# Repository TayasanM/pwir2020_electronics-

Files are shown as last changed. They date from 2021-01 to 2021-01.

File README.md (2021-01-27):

# pwir2020_Madmax_Electronics-
## Functionality Discription  
This electronic board consists of the main control circuit and driver circuit.  
  
This circuit capable of driver three DC Gear Motors (16V)  
  
and communicate with the onboard computer via USB connection execute Motor rotation is given speed and give feedback of speed.  
  
Another functionality of this board is controlling thrower servo Motor speed.  
  
Driver Motor speed control using PI controller implement in firmware to archive desired speed quickly  
## Communication  
Communication between the main PC and control board happens in HEX values(16 bits).  
driver Motor speeds send between 0-100, thrower Motors speed (0-1000) and end command  
  
Motor1_speed,Motor2_speed,Motor3_speed,Thrower_speed,command_end  
  
E.g. 64 00 64 00 64 00 64 00 AA AA  
  
## Connection ##  
- Micro USB: Communicate with PC where you can get speeds of the speeds of the motors and send feedback
- J7         : STM32 programmer connector  
	- 1 : +3.3V
	- 2 :SWDIO(communication with programmer)
	- 4 :SWCLK(Progrmamer clock)    
	- 10:NRST(reset)
	-  3,5,9:GND
	- 6,7,8: NC

- J5         : Driver Motor2 encoder conector
	- 1 : GND	    
	- 2 :+3.3V
	- 3 : Encoder Signal line 2 for Motor2
	- 4 : Encoder Signal line 1 for Motor2
             
- J6         : Driver Motor3 encoder conector
	- 1 : GND
	- 2 :+3.3V
	- 3 : Encoder Signal line 2 for Motor3
	- 4 : Encoder Signal line 1 for Motor3)
- J4         : Driver Motor1 encoder conector  
	- 1 : GND
	- 2 :+3.3V 
	- 3 : Encoder Signal line 2 for Motor1
	- 4 : Encoder Signal line 1 for Motor1
- J3         : Thrower Motor Signal connector
	-  1 : GND
	-  2  :PWM
	-  3 : NC 
	-  4 : NC
- U2         : Driver Motor1 power connector
- U3         : Driver Motor2 power connector
- U4         : Driver Motor3 power connector
- '+'          : Driver Motor powerconnection (battery 16V)
- '+'          : Driver Motor powerconnection (battery 16V)

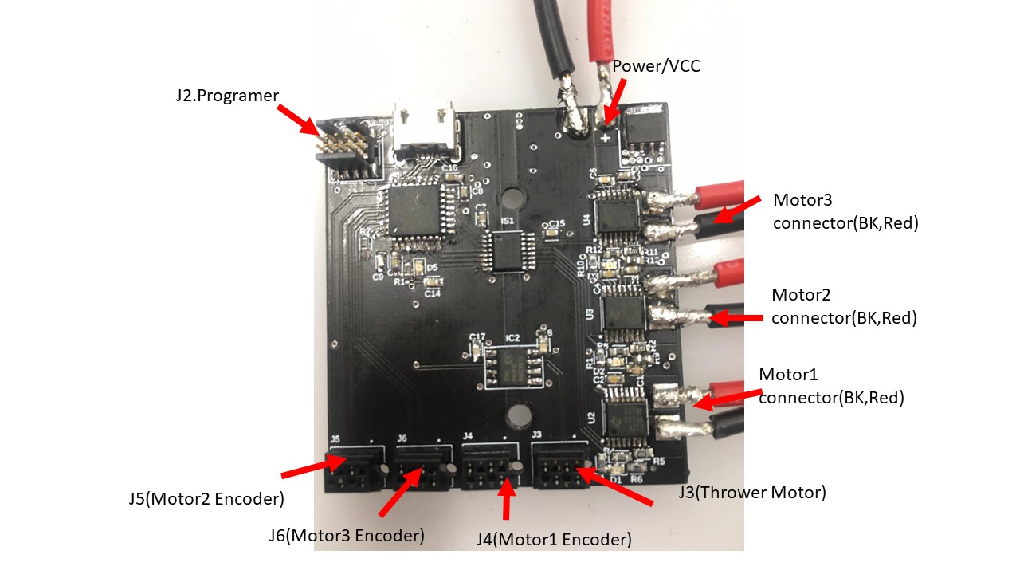
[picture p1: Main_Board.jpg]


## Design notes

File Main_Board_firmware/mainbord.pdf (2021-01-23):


07/12/2020

## mainbord Project Configuration Report

# 1. Description

## 1.1. Project

Project Name | mainbord
Board Name | custom
Generated with: | STM32CubeMX 6.0.0
Date | 12/07/2020

## 1.2. MCU

MCU Series | STM32G4
MCU Line | STM32G4x1
MCU name | STM32G431KBTx
MCU Package | LQFP32
MCU Pin number | 32

## 1.3. Core(s) information

Core(s) | ARM Cortex-M4

# 2. Pinout Configuration

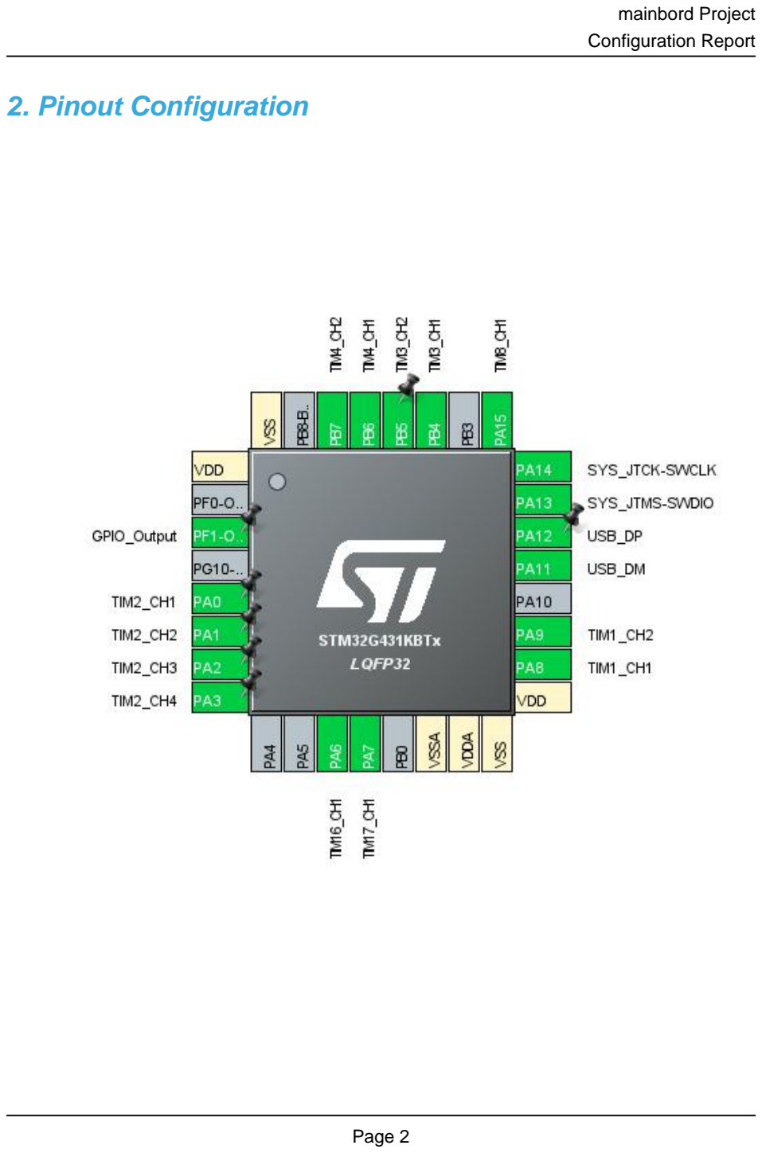
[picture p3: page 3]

# 3. Pins Configuration

Pin Number LQFP32 | Pin Name (function after reset) | Pin Type | Alternate Function(s) | Label
1 | VDD | Power
3 | PF1-OSC_OUT * | I/O | GPIO_Output
5 | PA0 | I/O | TIM2_CH1
6 | PA1 | I/O | TIM2_CH2
7 | PA2 | I/O | TIM2_CH3
8 | PA3 | I/O | TIM2_CH4
11 | PA6 | I/O | TIM16_CH1
12 | PA7 | I/O | TIM17_CH1
14 | VSSA | Power
15 | VDDA | Power
16 | VSS | Power
17 | VDD | Power
18 | PA8 | I/O | TIM1_CH1
19 | PA9 | I/O | TIM1_CH2
21 | PA11 | I/O | USB_DM
22 | PA12 | I/O | USB_DP
23 | PA13 | I/O | SYS_JTMS-SWDIO
24 | PA14 | I/O | SYS_JTCK-SWCLK
25 | PA15 | I/O | TIM8_CH1
27 | PB4 | I/O | TIM3_CH1
28 | PB5 | I/O | TIM3_CH2
29 | PB6 | I/O | TIM4_CH1
30 | PB7 | I/O | TIM4_CH2
32 | VSS | Power

## * The pin is affected with an I/O function

# 4. Clock Tree Configuration

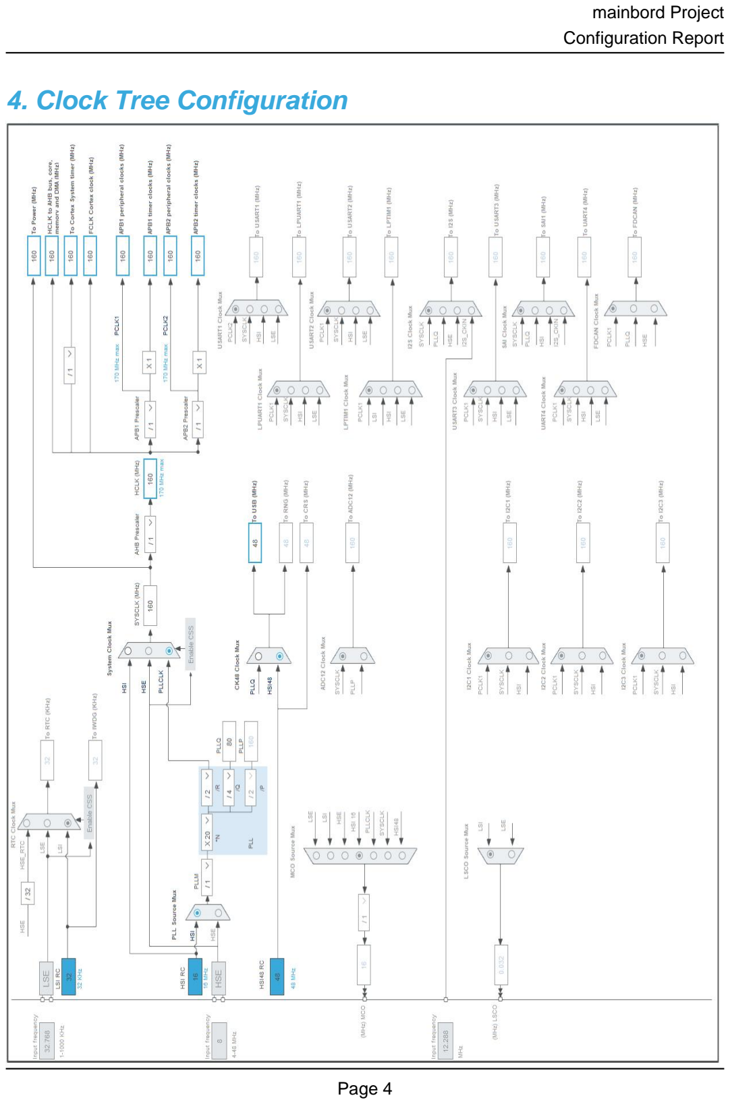
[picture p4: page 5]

# 5. Software Project

## 5.1. Project Settings

Name | Value
Project Name | mainbord
Project Folder | C:\Users\Dell\STM32CubeIDE\workspace_1.4.0\mainbord
Toolchain / IDE | STM32CubeIDE
Firmware Package Name and Version | STM32Cube FW_G4 V1.3.0
Application Structure | Advanced
Generate Under Root | Yes
Do not generate the main() | No
Minimum Heap Size | 0x200
Minimum Stack Size | 0x400

## 5.2. Code Generation Settings

Name | Value
STM32Cube MCU packages and embedded software | Copy only the necessary library files
Generate peripheral initialization as a pair of '.c/.h' files | No
Backup previously generated files when re-generating | No
Keep User Code when re-generating | Yes
Delete previously generated files when not re-generated | Yes
Set all free pins as analog (to optimize the power consumption) | No
Enable Full Assert | No

## 5.3. Advanced Settings - Generated Function Calls

Rank | Function Name | IP Instance Name
1 | MX_GPIO_Init | GPIO
2 | SystemClock_Config | RCC
3 | MX_TIM2_Init | TIM2
4 | MX_TIM3_Init | TIM3
5 | MX_TIM4_Init | TIM4
6 | MX_TIM7_Init | TIM7
7 | MX_TIM8_Init | TIM8
8 | MX_TIM1_Init | TIM1
9 | MX_TIM16_Init | TIM16
10 | MX_TIM17_Init | TIM17
11 | MX_USB_Device_Init | USB_DEVICE

Rank | Function Name | IP Instance Name
12 | MX_TIM6_Init | TIM6

# 6. Power Consumption Calculator report

## 6.1. Microcontroller Selection

Series | STM32G4
Line | STM32G4x1
MCU | STM32G431KBTx
Datasheet | DS12589_Rev0

## 6.2. Parameter Selection

Temperature | 25
Vdd | 3.0

## 6.3. Battery Selection

Battery | Li-SOCL2(A3400)
Capacity | 3400.0 mAh
Self Discharge | 0.08 %/month
Nominal Voltage | 3.6 V
Max Cont Current | 100.0 mA
Max Pulse Current | 200.0 mA
Cells in series | 1
Cells in parallel | 1

## 6.4. Sequence

Step | Step1 | Step2
Mode | RUN | STOP1
Vdd | 3.0 | 3.0
Voltage Source | Battery | Battery
Range | Range1-Boost | NoRange
Fetch Type | FLASH/ART | NA
CPU Frequency | 170 MHz | 0 Hz
Clock Configuration | HSE BYP PLL | ALL CLOCKS OFF
Clock Source Frequency | 4 MHz | 0 Hz

### Peripherals

Additional Cons. | 0 mA | 0 mA
Average Current | 25.5 mA | 59 µA
Duration | 0.1 ms | 0.9 ms
DMIPS | 213.0 | 0.0
Ta Max | 124.19 | 129.99
Category | In DS Table | In DS Table

## 6.5. Results

Sequence Time | 1 ms | Average Current | 2.6 mA
Battery Life | 1 month, 23 days, 22 hours | Average DMIPS | 212.5 DMIPS

## 6.6. Chart

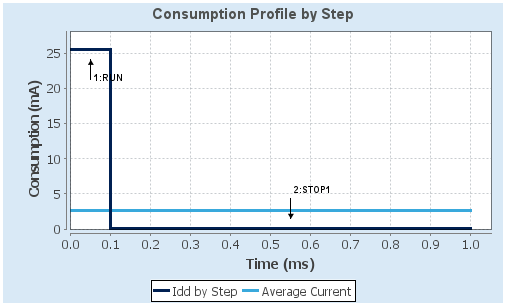
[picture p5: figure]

# 7. IPs and Middleware Configuration

## 7.1. GPIO

## 7.2. RCC

## 7.2.1. Parameter Settings:

### System Parameters:

VDD voltage (V) | 3.3
Instruction Cache | Enabled
Prefetch Buffer | Disabled
Data Cache | Enabled
Flash Latency(WS) | 4 WS (5 CPU cycle)

### RCC Parameters:

HSI Calibration Value | 64
HSE Startup Timout Value (ms) | 100
LSE Startup Timout Value (ms) | 5000

### Power Parameters:

Power Regulator Voltage Scale | Power Regulator Voltage Scale 1 boost

### Peripherals Clock Configuration:

Generate the peripherals clock configuration | TRUE

## 7.3. SYS Debug: Serial Wire Timebase Source: SysTick mode: save power of non-active UCPD - deactive Dead Battery pull-up

## 7.4. TIM1 Combined Channels: Encoder Mode

## 7.4.1. Parameter Settings:

### Counter Settings:

Prescaler (PSC - 16 bits value) | 0
Counter Mode | Up
Dithering | Disable
Counter Period (AutoReload Register - 16 bits value ) | 65535
Internal Clock Division (CKD) | No Division
Repetition Counter (RCR - 16 bits value) | 0

auto-reload preload | Disable

### Trigger Output (TRGO) Parameters:

Master/Slave Mode (MSM bit) | Disable (Trigger input effect not delayed)
Trigger Event Selection TRGO | Reset (UG bit from TIMx_EGR)
Trigger Event Selection TRGO2 | Reset (UG bit from TIMx_EGR)

### Pulse On Compare ( Common for Channel 3 and 4 ):

Pulse Width Prescaler | 0
Pulse Width | 0

### Encoder:

Encoder Mode | Encoder Mode TI1 and TI2 *
Slave Mode Preload Activation | Disable
____ Parameters for Channel 1 ____
Polarity | Rising Edge
IC Selection | Direct
Prescaler Division Ratio | No division
Input Filter | 0
____ Parameters for Channel 2 ____
Polarity | Rising Edge
IC Selection | Direct
Prescaler Division Ratio | No division
Input Filter | 0

## 7.5. TIM2 Channel1: PWM Generation CH1 Channel2: PWM Generation CH2 Channel3: PWM Generation CH3 Channel4: PWM Generation CH4

## 7.5.1. Parameter Settings:

### Counter Settings:

Prescaler (PSC - 16 bits value) | 0
Counter Mode | Up
Dithering | Disable
Counter Period (AutoReload Register - 32 bits value ) | 65535 *
Internal Clock Division (CKD) | No Division
auto-reload preload | Disable

### Trigger Output (TRGO) Parameters:

Master/Slave Mode (MSM bit) | Disable (Trigger input effect not delayed)
Trigger Event Selection TRGO | Reset (UG bit from TIMx_EGR)

### Clear Input:

Clear Input Source | Disable

### Pulse On Compare ( Common for Channel 3 and 4 ):

Pulse Width Prescaler | 0
Pulse Width | 0

### PWM Generation Channel 1:

Mode | PWM mode 1
Pulse (32 bits value) | 0
Output compare preload | Enable
Fast Mode | Disable
CH Polarity | High

### PWM Generation Channel 2:

Mode | PWM mode 1
Pulse (32 bits value) | 0
Output compare preload | Enable
Fast Mode | Disable
CH Polarity | High

### PWM Generation Channel 3:

Mode | PWM mode 1
Pulse (32 bits value) | 0
Output compare preload | Enable
Fast Mode | Disable
CH Polarity | High

### PWM Generation Channel 4:

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

## 7.6. TIM3 Combined Channels: Encoder Mode

## 7.6.1. Parameter Settings:

### Counter Settings:

Prescaler (PSC - 16 bits value) | 0
Counter Mode | Up
Dithering | Disable
Counter Period (AutoReload Register - 16 bits value ) | 65535

Internal Clock Division (CKD) | No Division
auto-reload preload | Disable

### Trigger Output (TRGO) Parameters:

Master/Slave Mode (MSM bit) | Disable (Trigger input effect not delayed)
Trigger Event Selection TRGO | Reset (UG bit from TIMx_EGR)

### Pulse On Compare ( Common for Channel 3 and 4 ):

Pulse Width Prescaler | 0
Pulse Width | 0

### Encoder:

Encoder Mode | Encoder Mode TI1 and TI2 *
Slave Mode Preload Activation | Disable
____ Parameters for Channel 1 ____
Polarity | Rising Edge
IC Selection | Direct
Prescaler Division Ratio | No division
Input Filter | 0
____ Parameters for Channel 2 ____
Polarity | Rising Edge
IC Selection | Direct
Prescaler Division Ratio | No division
Input Filter | 0

## 7.7. TIM4 Combined Channels: Encoder Mode

## 7.7.1. Parameter Settings:

### Counter Settings:

Prescaler (PSC - 16 bits value) | 0
Counter Mode | Up
Dithering | Disable
Counter Period (AutoReload Register - 16 bits value ) | 65535
Internal Clock Division (CKD) | No Division
auto-reload preload | Disable

### Trigger Output (TRGO) Parameters:

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

### Pulse On Compare ( Common for Channel 3 and 4 ):

Pulse Width Prescaler | 0
Pulse Width | 0

### Encoder:

Encoder Mode | Encoder Mode TI1 and TI2 *
Slave Mode Preload Activation | Disable
____ Parameters for Channel 1 ____
Polarity | Rising Edge
IC Selection | Direct
Prescaler Division Ratio | No division
Input Filter | 0
____ Parameters for Channel 2 ____
Polarity | Rising Edge
IC Selection | Direct
Prescaler Division Ratio | No division
Input Filter | 0

## 7.8. TIM6 mode: Activated

## 7.8.1. Parameter Settings:

### Counter Settings:

Prescaler (PSC - 16 bits value) | 24 *
Counter Mode | Up
Dithering | Disable
Counter Period (AutoReload Register - 16 bits value ) | 63999 *
auto-reload preload | Disable

### Trigger Output (TRGO) Parameters:

Trigger Event Selection | Reset (UG bit from TIMx_EGR)

## 7.9. TIM7 mode: Activated

## 7.9.1. Parameter Settings:

### Counter Settings:

Prescaler (PSC - 16 bits value) | 0
Counter Mode | Up
Dithering | Disable
Counter Period (AutoReload Register - 16 bits value ) | 65535
auto-reload preload | Disable

### Trigger Output (TRGO) Parameters:

Trigger Event Selection | Reset (UG bit from TIMx_EGR)

## 7.10. TIM8 Channel1: PWM Generation CH1

## 7.10.1. Parameter Settings:

### Counter Settings:

Prescaler (PSC - 16 bits value) | 0
Counter Mode | Up
Dithering | Disable
Counter Period (AutoReload Register - 16 bits value ) | 65535
Internal Clock Division (CKD) | No Division
Repetition Counter (RCR - 16 bits value) | 0
auto-reload preload | Disable

### Trigger Output (TRGO) Parameters:

Master/Slave Mode (MSM bit) | Disable (Trigger input effect not delayed)
Trigger Event Selection TRGO | Reset (UG bit from TIMx_EGR)
Trigger Event Selection TRGO2 | Reset (UG bit from TIMx_EGR)

### Break And Dead Time management - BRK Configuration:

BRK State | Disable
BRK Polarity | High
BRK Filter (4 bits value) | 0
BRK Sources Configuration
- Digital Input | Disable
- COMP1 | Disable
- COMP2 | Disable
- COMP3 | Disable
- COMP4 | Disable

### Break And Dead Time management - BRK2 Configuration:

BRK2 State | Disable
BRK2 Polarity | High
BRK2 Filter (4 bits value) | 0
BRK2 Sources Configuration
- Digital Input | Disable
- COMP1 | Disable
- COMP2 | Disable
- COMP3 | Disable
- COMP4 | Disable

### Break And Dead Time management - Output Configuration:

Automatic Output State | Disable
Off State Selection for Run Mode (OSSR) | Disable
Off State Selection for Idle Mode (OSSI) | Disable
Lock Configuration | Off

### Clear Input:

Clear Input Source | Disable

### Pulse On Compare ( Common for Channel 3 and 4 ):

Pulse Width Prescaler | 0
Pulse Width | 0

### PWM Generation Channel 1:

Mode | PWM mode 1
Pulse (16 bits value) | 0
Output compare preload | Enable
Fast Mode | Disable
CH Polarity | High
CH Idle State | Reset

## 7.11. TIM16 mode: Activated Channel1: PWM Generation CH1

## 7.11.1. Parameter Settings:

### Counter Settings:

Prescaler (PSC - 16 bits value) | 0
Counter Mode | Up
Dithering | Disable
Counter Period (AutoReload Register - 16 bits value ) | 65535
Internal Clock Division (CKD) | No Division
Repetition Counter (RCR - 8 bits value) | 0
auto-reload preload | Disable

### Break And Dead Time management - BRK Configuration:

BRK State | Disable
BRK Polarity | High
BRK Filter (4 bits value) | 0
BRK Sources Configuration
- Digital Input | Disable
- COMP1 | Disable
- COMP2 | Disable
- COMP3 | Disable
- COMP4 | Disable

### Break And Dead Time management - Output Configuration:

Automatic Output State | Disable
Off State Selection for Run Mode (OSSR) | Disable
Off State Selection for Idle Mode (OSSI) | Disable
Lock Configuration | Off

### PWM Generation Channel 1:

Mode | PWM mode 1
Pulse (16 bits value) | 0
Output compare preload | Enable
Fast Mode | Disable
CH Polarity | High
CH Idle State | Reset

## 7.12. TIM17 mode: Activated Channel1: PWM Generation CH1

## 7.12.1. Parameter Settings:

### Counter Settings:

Prescaler (PSC - 16 bits value) | 0
Counter Mode | Up
Dithering | Disable
Counter Period (AutoReload Register - 16 bits value ) | 65535
Internal Clock Division (CKD) | No Division
Repetition Counter (RCR - 8 bits value) | 0
auto-reload preload | Disable

### Break And Dead Time management - BRK Configuration:

BRK State | Disable
BRK Polarity | High
BRK Filter (4 bits value) | 0
BRK Sources Configuration
- Digital Input | Disable
- COMP1 | Disable
- COMP2 | Disable
- COMP3 | Disable
- COMP4 | Disable

### Break And Dead Time management - Output Configuration:

Automatic Output State | Disable
Off State Selection for Run Mode (OSSR) | Disable
Off State Selection for Idle Mode (OSSI) | Disable

Lock Configuration | Off

### PWM Generation Channel 1:

Mode | PWM mode 1
Pulse (16 bits value) | 0
Output compare preload | Enable
Fast Mode | Disable
CH Polarity | High
CH Idle State | Reset

## 7.13. USB mode: Device (FS)

## 7.13.1. Parameter Settings:

### Basic Parameters:

Speed | Full Speed 12MBit/s
Physical interface | Internal Phy
Sof Enable | Disabled

### Power Parameters:

Low Power | Disabled
Link Power Management | Disabled
Battery Charging | Disabled

## 7.14. USB_DEVICE Class For FS IP: Communication Device Class (Virtual Port Com)

## 7.14.1. Parameter Settings:

### Basic Parameters:

USBD_MAX_NUM_INTERFACES (Maximum number of supported interfaces) | 1
USBD_MAX_NUM_CONFIGURATION (Maximum number of supported configuration) | 1
USBD_MAX_STR_DESC_SIZ (Maximum size for the string descriptors) | 512
USBD_SELF_POWERED (Enabled self power) | Enabled
USBD_DEBUG_LEVEL (USBD Debug Level) | 0: No debug message
USBD_LPM_ENABLED (Link Power Management) | 1: Link Power Management supported

### Class Parameters:

USB CDC Rx Buffer Size | 1000
USB CDC Tx Buffer Size | 1000

## 7.14.2. Device Descriptor:

### Device Descriptor:

VID (Vendor IDentifier) | 1155
LANGID_STRING (Language Identifier) | English(United States)
MANUFACTURER_STRING (Manufacturer Identifier) | STMicroelectronics

### Device Descriptor FS:

PID (Product IDentifier) | 22336
PRODUCT_STRING (Product Identifier) | STM32 Virtual ComPort
CONFIGURATION_STRING (Configuration Identifier) | CDC Config
INTERFACE_STRING (Interface Identifier) | CDC Interface

### * User modified value

# 8. System Configuration

## 8.1. GPIO configuration

IP | Pin | Signal | GPIO mode | GPIO pull/up pull down | Max Speed | User Label
SYS | PA13 | SYS_JTMS-SWDIO | n/a | n/a | n/a
| PA14 | SYS_JTCK-SWCLK | n/a | n/a | n/a
TIM1 | PA8 | TIM1_CH1 | Alternate Function Push Pull | No pull-up and no pull-down | Low
| PA9 | TIM1_CH2 | Alternate Function Push Pull | No pull-up and no pull-down | Low
TIM2 | PA0 | TIM2_CH1 | Alternate Function Push Pull | No pull-up and no pull-down | Low
| PA1 | TIM2_CH2 | Alternate Function Push Pull | No pull-up and no pull-down | Low
| PA2 | TIM2_CH3 | Alternate Function Push Pull | No pull-up and no pull-down | Low
| PA3 | TIM2_CH4 | Alternate Function Push Pull | No pull-up and no pull-down | Low
TIM3 | PB4 | TIM3_CH1 | Alternate Function Push Pull | No pull-up and no pull-down | Low
| PB5 | TIM3_CH2 | Alternate Function Push Pull | No pull-up and no pull-down | Low
TIM4 | PB6 | TIM4_CH1 | Alternate Function Push Pull | No pull-up and no pull-down | Low
| PB7 | TIM4_CH2 | Alternate Function Push Pull | No pull-up and no pull-down | Low
TIM8 | PA15 | TIM8_CH1 | Alternate Function Push Pull | No pull-up and no pull-down | Low
TIM16 | PA6 | TIM16_CH1 | Alternate Function Push Pull | No pull-up and no pull-down | Low
TIM17 | PA7 | TIM17_CH1 | Alternate Function Push Pull | No pull-up and no pull-down | Low
USB | PA11 | USB_DM | n/a | n/a | n/a
| PA12 | USB_DP | n/a | n/a | n/a
GPIO | PF1-OSC_OUT | GPIO_Output | Output Push Pull | No pull-up and no pull-down | Low

## 8.2. DMA configuration

## nothing configured in DMA service

## 8.3. NVIC configuration

## 8.3.1. NVIC

Interrupt Table | Enable | Preenmption Priority | SubPriority
Non maskable interrupt | true | 0 | 0
Hard fault interrupt | true | 0 | 0
Memory management fault | true | 0 | 0
Prefetch fault, memory access fault | true | 0 | 0
Undefined instruction or illegal state | true | 0 | 0
System service call via SWI instruction | true | 0 | 0
Debug monitor | true | 0 | 0
Pendable request for system service | true | 0 | 0
System tick timer | true | 0 | 0
USB low priority interrupt remap | true | 0 | 0
TIM6 global interrupt, DAC1 and DAC3 channel underrun error interrupts | true | 0 | 0
PVD/PVM1/PVM2/PVM3/PVM4 interrupts through EXTI lines 16/38/39/40/41 | unused
Flash global interrupt | unused
RCC global interrupt | unused
USB high priority interrupt remap | unused
TIM1 break interrupt and TIM15 global interrupt | unused
TIM1 update interrupt and TIM16 global interrupt | unused
TIM1 trigger and commutation interrupts and TIM17 global interrupt | unused
TIM1 capture compare interrupt | unused
TIM2 global interrupt | unused
TIM3 global interrupt | unused
TIM4 global interrupt | unused
TIM8 break interrupt | unused
TIM8 update interrupt | unused
TIM8 trigger and commutation interrupts | unused
TIM8 capture compare interrupt | unused
TIM7 global interrupt | unused
FPU global interrupt | unused

## 8.3.2. NVIC Code generation

Enabled interrupt Table | Select for init sequence ordering | Generate IRQ handler | Call HAL handler
Non maskable interrupt | true | true | false
Hard fault interrupt | true | true | false

Enabled interrupt Table | Select for init sequence ordering | Generate IRQ handler | Call HAL handler
Memory management fault | true | true | false
Prefetch fault, memory access fault | true | true | false
Undefined instruction or illegal state | true | true | false
System service call via SWI instruction | true | true | false
Debug monitor | true | true | false
Pendable request for system service | true | true | false
System tick timer | true | true | true
USB low priority interrupt remap | true | true | true
TIM6 global interrupt, DAC1 and DAC3 channel underrun error interrupts | true | true | true

### * User modified value

# 9. System Views

## 9.1. Category view 9.1.1. Current

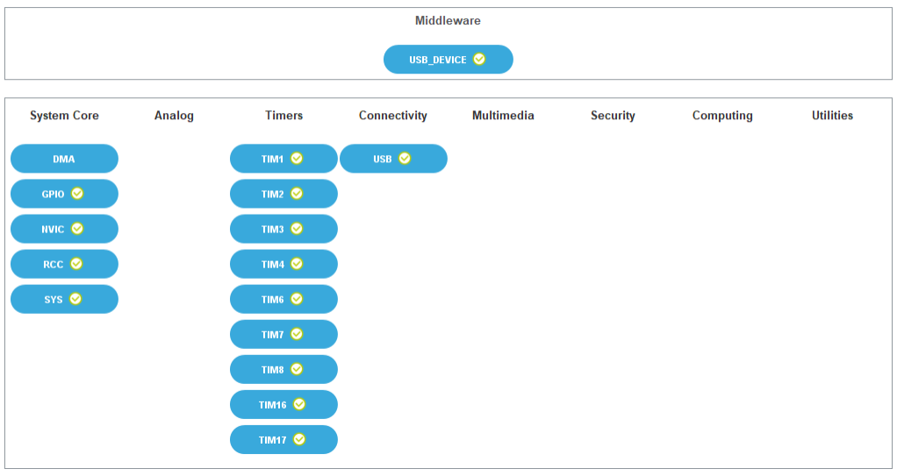
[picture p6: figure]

# 10. Software Pack Report

## 10.1. Software Pack selected

Vendor | Name | Version | Component
STMicroelectronic s | USB_DEVICE | 3.0.0 | Class : USB Group : USB Device SubGroup : CDC FS Version : 3.0

# 11. Docs & Resources

Type | Link
Datasheet | http://www.st.com/resource/en/datasheet/DM00507199.pdf
Reference manual | http://www.st.com/resource/en/reference_manual/DM00355726.pdf
Programming manual | http://www.st.com/resource/en/programming_manual/DM00046982.pdf
Errata sheet | http://www.st.com/resource/en/errata_sheet/DM00502298.pdf
Application note | http://www.st.com/resource/en/application_note/CD00160362.pdf
Application note | http://www.st.com/resource/en/application_note/CD00167594.pdf
Application note | http://www.st.com/resource/en/application_note/CD00259245.pdf
Application note | http://www.st.com/resource/en/application_note/CD00264342.pdf
Application note | http://www.st.com/resource/en/application_note/CD00264379.pdf
Application note | http://www.st.com/resource/en/application_note/DM00042534.pdf
Application note | http://www.st.com/resource/en/application_note/DM00072315.pdf
Application note | http://www.st.com/resource/en/application_note/DM00074240.pdf
Application note | http://www.st.com/resource/en/application_note/DM00081379.pdf
Application note | http://www.st.com/resource/en/application_note/DM00083249.pdf
Application note | http://www.st.com/resource/en/application_note/DM00129215.pdf
Application note | http://www.st.com/resource/en/application_note/DM00151811.pdf
Application note | http://www.st.com/resource/en/application_note/DM00257177.pdf
Application note | http://www.st.com/resource/en/application_note/DM00272912.pdf
Application note | http://www.st.com/resource/en/application_note/DM00226326.pdf
Application note | http://www.st.com/resource/en/application_note/DM00355687.pdf
Application note | http://www.st.com/resource/en/application_note/DM00311483.pdf
Application note | http://www.st.com/resource/en/application_note/DM00380469.pdf
Application note | http://www.st.com/resource/en/application_note/DM00395696.pdf
Application note | http://www.st.com/resource/en/application_note/DM00493651.pdf
Application note | http://www.st.com/resource/en/application_note/DM00535045.pdf

Application note | http://www.st.com/resource/en/application_note/DM00536349.pdf
Application note | http://www.st.com/resource/en/application_note/DM00605707.pdf
Application note | http://www.st.com/resource/en/application_note/DM00607955.pdf
Application note | http://www.st.com/resource/en/application_note/DM00610467.pdf
Application note | http://www.st.com/resource/en/application_note/DM00625282.pdf
Application note | http://www.st.com/resource/en/application_note/DM00442716.pdf
Application note | http://www.st.com/resource/en/application_note/DM00625700.pdf
Application note | http://www.st.com/resource/en/application_note/DM00442720.pdf

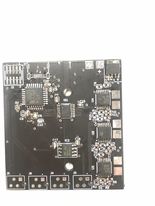
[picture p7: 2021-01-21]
141259562_133307985303833_5462991217890036333_n.jpg

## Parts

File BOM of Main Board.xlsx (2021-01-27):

 |  |  |  | Suppler
Qty | Component Name | Comment | Designators | Mouser | Farnell | TME
1 | STM32G431KB | LQFP-32 | Microcontroller | 511-STM32G431KBT6 (https://www.mouser.ee/ProductDetail/STMicroelectronics/STM32G431KBT6?qs=T3oQrply3y8teCTeNAFOLg%3D%3D) | 3132405 (https://ee.farnell.com/stmicroelectronics/stm32g431kbt6/mcu-32bit-170mhz-lqfp-32/dp/3132405)
3 | DRV8874 |  | Motor Driver | 595-DRV8874QPWPRQ1 (https://www.mouser.ee/ProductDetail/Texas-Instruments/DRV8874QPWPRQ1?qs=mAH9sUMRCttZUT1myh3Itg%3D%3D)
1 | SI8660BB-B-IU | Isolator(6 channel Forawad)/QSOP-16 | isolate micro controller PWM signal from Driver side | 634-SI8660BB-B-IU (https://www.mouser.ee/ProductDetail/Silicon-Labs/SI8660BB-B-IU?qs=1mbolxNpo8divSWJ7idUTg%3D%3D) | 3105912 (https://ee.farnell.com/silicon-labs/si8660bb-b-iu/digital-isolator-6ch-40-to-125deg/dp/3105912)
1 | SI8620BB-B-IS | Isolator(2 channel unidirection)/SOIC-8) | isolate micro controller PWM to Thrower Motor control | 634-SI8620BB-B-ISR (https://www.mouser.ee/ProductDetail/Silicon-Labs/SI8620BB-B-ISR?qs=j6MGy4L9yX3UqdNjYI%2FCRQ%3D%3D) | 2423240 (https://ee.farnell.com/silicon-labs/si8620bb-b-is/digital-isolator-8ns-nsoic-8/dp/2423240) | SI8620BB-B-IS (https://www.tme.eu/ee/details/si8620bb-b-is/integraallulitused-muud-kasutajaliid/silicon-labs/)
4 | Micro-MaTch 215079-4 | Recommended encoder connector | connect encoders of the Motors and thrower PWM and ground | 571-215079-4 (https://www.mouser.ee/ProductDetail/TE-Connectivity-AMP/215079-4) | 1772996 (https://ee.farnell.com/amp-te-connectivity/215079-4/connector-4way-vertical-1-27/dp/1772996) | 7-215079-4 (https://www.tme.eu/ee/details/7-215079-4/uhendused-micro-match-raster-1-27mm/te-connectivity/)
1 | FTSH-105-01-L-DV-K | Recommended programmer connector |  | 200-FTSH10501LDVK (https://www.mouser.ee/ProductDetail/Samtec/FTSH-105-01-L-DV-K?qs=%252B5JSS813miOqo3Vy%252BvhCFg%3D%3D) | 2856437 (https://ee.farnell.com/samtec/ftsh-105-01-l-dv-k-p/connector-header-10pos-2row-1/dp/2856437)
1 | Würth Elektronik 629105150521 | Micro USB Type B Connectors | USB connector to comuncate via USB | 710-629105150521 (https://www.mouser.ee/ProductDetail/Wurth-Elektronik/629105150521/) | 2470822
1 | Würth Elektronik 824011 TVS Diode | SOT-23-5/2 channel | High speed communicate and proector to USB commincations | 710-824011 (https://www.mouser.ee/ProductDetail/Wurth-Elektronik/824011/?qs=Wn16VcyqZWrHR48Vn%2FB8%252Bg%3D%3D) | 1748616
1 | TLV702 | 3.3V output, SOT23-5 | Power to micro contoer side input 5V | 595-TLV70233DBVR (https://www.mouser.ee/ProductDetail/Texas-Instruments/TLV70233DBVR/?qs=zQ2yIHQ6k3wiHrD0NUI05Q==) | 3007784 | TLV70233DBVR
1 | TPS709B345DBVR | 5V output, SOT23-5 | Power driver IC and isolateros input 16V | 595-TPS709B345DBVR (https://www.mouser.ee/ProductDetail/Texas-Instruments/TPS709B345DBVR/?qs=B6kkDfuK7%2FBdmmT4wtT%252BGA==)
1 | BUK6Y10-30P | Supply MOSFET |  | 771-BUK6Y10-30PX (https://eu.mouser.com/ProductDetail/Nexperia/BUK6Y10-30PX?qs=vmHwEFxEFR9UKLhknfc3PQ==) | 3438512
6 | 100k | R_CHIP-0603(1608-METRIC)
14 | 100n | C_CHIP-0603(1608-METRIC)
1 | 10k | R_CHIP-0603(1608-METRIC)
15 | 10u | C_CHIP-1206(3216-METRIC)
2 | 1u | C_CHIP-0603(1608-METRIC)
3 | 2.2k | R_CHIP-0603(1608-METRIC)
2 | 2.2u | C_CHIP-0603(1608-METRIC)
5 | 2.7k | R_CHIP-0603(1608-METRIC)
3 | 22n | C_CHIP-0603(1608-METRIC)
1 | 4.7u | C_CHIP-0603(1608-METRIC)
5 | LED_RED | LED_CHIP_RED-1608

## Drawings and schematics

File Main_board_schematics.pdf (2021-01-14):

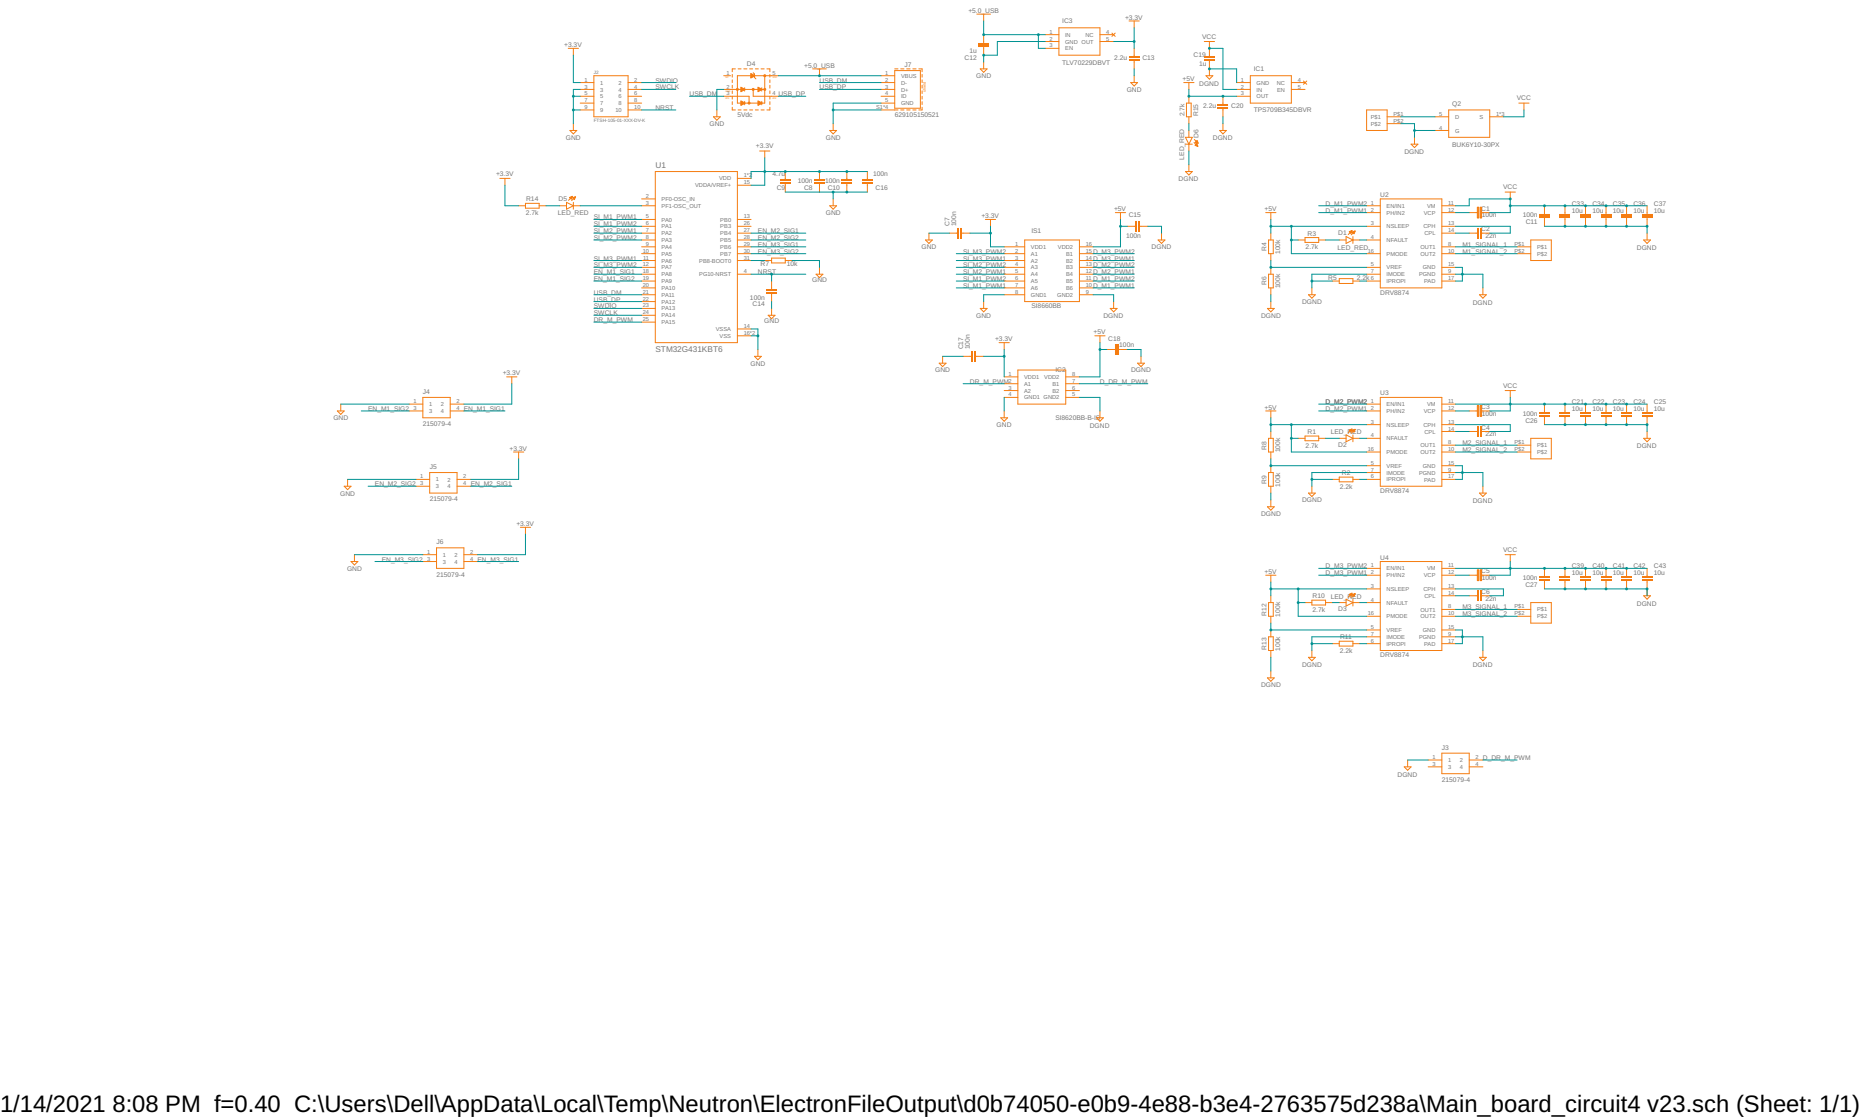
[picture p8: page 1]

1/14/2021 8:08 PM f=0.40 C:\Users\Dell\AppData\Local\Temp\Neutron\ElectronFileOutput\d0b74050-e0b9-4e88-b3e4-2763575d238a\Main_board_circuit4 v23.sch (Sheet: 1/1)

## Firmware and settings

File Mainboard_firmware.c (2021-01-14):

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
/* Includes ------------------------------------------------------------------*/
#include "main.h"
#include "usb_device.h"

TIM_HandleTypeDef htim1;
TIM_HandleTypeDef htim2;
TIM_HandleTypeDef htim3;
TIM_HandleTypeDef htim4;
TIM_HandleTypeDef htim6;
TIM_HandleTypeDef htim7;
TIM_HandleTypeDef htim8;
TIM_HandleTypeDef htim16;
TIM_HandleTypeDef htim17;

void SystemClock_Config(void);
static void MX_GPIO_Init(void);
static void MX_TIM2_Init(void);
static void MX_TIM3_Init(void);
static void MX_TIM4_Init(void);
static void MX_TIM7_Init(void);
static void MX_TIM8_Init(void);
static void MX_TIM1_Init(void);
static void MX_TIM16_Init(void);
static void MX_TIM17_Init(void);
static void MX_TIM6_Init(void);
/* USER CODE BEGIN 0 */
typedef struct Command { // (1)
  int16_t speed1;
  int16_t speed2;
  int16_t speed3;
  uint16_t throwerSpeed;
  //uint16_t kp;
  uint16_t delimiter; // (2)
} Command;
Command command = {.speed1 = 0, .speed2 = 0, .speed3 = 0, .throwerSpeed = 0,.delimiter = 0}; // (4)
volatile uint8_t isCommandReceived = 0; // (5)


typedef struct PID {
  int16_t position;
  int16_t positionChange;
  int16_t setpoint;
  int16_t positionPrev;
  int32_t ErrorPrev;
  float Cum_error;
  int32_t Error;
  int32_t Errorchange;
  int32_t kp;
  uint32_t ki;
  uint32_t kd;
  uint32_t U;
  int32_t P;
  int32_t I;
  int32_t D;
  int32_t PID;




} PID;

int32_t getPID(PID* pid,int16_t newPosition){
	  pid->kp=8000;
	  pid->ki=50;
	  pid->kd=0;
	  pid->positionPrev = pid->position;
	  pid->position = newPosition;
	  pid->positionChange=pid->position-pid->positionPrev;
	  pid->Error =(pid->setpoint)-(pid->positionChange);

	  pid->P=(pid->kp*pid->Error);

	  pid->Cum_error=pid->Cum_error+pid->Error;
	  if(pid->setpoint==0)
	  {
		  pid->Cum_error=0;
	  }
	  if(pid->Cum_error>3500)
	 	  {
	 		  pid->Cum_error=3500;
	 	  }
	  if(pid->Cum_error<-3500)
	 	  {
	 		  pid->Cum_error=-3500;
	 	  }
	  pid->I=pid->ki*pid->Cum_error;

	  pid->Errorchange=pid->Error-pid->ErrorPrev;
	  pid->ErrorPrev=pid->Error;
	  pid->D=(pid->kd*pid->Errorchange);

	  pid->PID=pid->P+pid->I;//+pid->D;




	  return pid->PID;


}
int32_t getthowerspeed(int speed)
{
	if(speed==0)
	{
		speed=3000;
	}
	else
	{
		speed=3000+33*speed;
	}
	return speed;
}

typedef struct Feedback { // (3)
  int16_t speed1;
  uint16_t error;
  int16_t speed2;
  int16_t speed3;
  uint16_t delimiter;

} Feedback;



void CDC_On_Receive(uint8_t* buffer, uint32_t* length) { // (6)

	if (*length == sizeof(Command)) { // (7)
    memcpy(&command, buffer, sizeof(Command)); // (8)

    if (command.delimiter == 0xAAAA) { // (9)
      isCommandReceived = 1;
    }
  }
}

PID Motor1 = { .position=0,.positionChange=0,.setpoint=0,.positionPrev=0,.Cum_error=0,.D=0,.Error=0,.ErrorPrev=0l,.Errorchange=0,.I=0,.kp=0,.ki=0,.kd=0,.PID=0,};
PID Motor2 = { .position=0};
PID Motor3 =  { .position=0};
void Motor_control_calculations(){
	int32_t PID1;int32_t PID2;int32_t PID3;


	PID1  = getPID(&Motor1,(int16_t)TIM1->CNT);
	PID2  = getPID(&Motor2,(int16_t)TIM3->CNT);
	PID3  = getPID(&Motor3,(int16_t)TIM4->CNT);
//	TIM2->CCR1 = 65535;
//	TIM2->CCR2 =0;
//	TIM2->CCR3 = 65535;
//	TIM2->CCR4 = 0;
//	TIM17->CCR1 = 65535;
//	TIM16->CCR1 = 0;

	if (PID1 > 65535)
	{
	    PID1 = 65535;
	}
	else if (PID1 < -65535)
	{
	    PID1 = -65535;
	}
	if (PID2 > 65535)
	{
		PID2 = 65535;
	}
	else if (PID2 < -65535)
	{
		PID2 = -65535;
	}
	if (PID3 > 65535)
	{
		PID3 = 65535;
	}
	else if (PID3 < -65535)
	{
		PID3 = -65535;
	}
	if(PID1>0){
			TIM2->CCR2 = PID1;
			TIM2->CCR1 = 0;
		}
	else{
			TIM2->CCR1 = -PID1;
			TIM2->CCR2 = 0;
		}
	if(PID2>0){
			TIM2->CCR4 = PID2;
			TIM2->CCR3 = 0;
			}
	else{
			TIM2->CCR3 = -PID2;
			TIM2->CCR4 = 0;
		}
	if(PID3>0){
			TIM17->CCR1 = PID3;
			TIM16->CCR1 = 0;
				}
	else{
			TIM16->CCR1 = -PID3;
			TIM17->CCR1 = 0;
		}
}


void HAL_TIM_PeriodElapsedCallback(TIM_HandleTypeDef *htim) {
	  Motor_control_calculations(); // Motor control calculations can be called from here
 }
/* USER CODE END 0 */

/**
  * @brief  The application entry point.
  * @retval int
  */
int main(void)
{
  /* MCU Configuration--------------------------------------------------------*/

  /* Reset of all peripherals, Initializes the Flash interface and the Systick. */
  HAL_Init();

  /* Configure the system clock */
  SystemClock_Config();

  /* Initialize all configured peripherals */
  MX_GPIO_Init();
  MX_TIM2_Init();
  MX_TIM3_Init();
  MX_TIM4_Init();
  MX_TIM7_Init();
  MX_TIM8_Init();
  MX_TIM1_Init();
  MX_TIM16_Init();
  MX_TIM17_Init();
  MX_USB_Device_Init();
  MX_TIM6_Init();
  /* USER CODE BEGIN 2 */
  Feedback feedback = { // (1)
       .speed1 = 0,
       .speed2 = 0,
       .speed3 = 0,
	   .error=0,
       .delimiter = 0xAAAA
   };

  HAL_TIM_Encoder_Start(&htim1, TIM_CHANNEL_1 | TIM_CHANNEL_2);
  HAL_TIM_Encoder_Start(&htim3, TIM_CHANNEL_1 | TIM_CHANNEL_2);
  HAL_TIM_Encoder_Start(&htim4, TIM_CHANNEL_1 | TIM_CHANNEL_2);
  HAL_TIM_Base_Start_IT(&htim6);
  HAL_TIM_PWM_Start(&htim2, TIM_CHANNEL_1);
  HAL_TIM_PWM_Start(&htim2, TIM_CHANNEL_2);
  HAL_TIM_PWM_Start(&htim2, TIM_CHANNEL_3);
  HAL_TIM_PWM_Start(&htim2, TIM_CHANNEL_4);//| TIM_CHANNEL_2 | TIM_CHANNEL_3 | TIM_CHANNEL_4);
  HAL_TIM_PWM_Start(&htim16, TIM_CHANNEL_1);
  HAL_TIM_PWM_Start(&htim17, TIM_CHANNEL_1);
  HAL_TIM_PWM_Start(&htim8, TIM_CHANNEL_1);
  TIM8->CCR1=3000;
  /* USER CODE END 2 */

  /* Infinite loop */
  /* USER CODE BEGIN WHILE */
  while (1)
  {
    /* USER CODE END WHILE */

    /* USER CODE BEGIN 3 */
	  if (isCommandReceived) { // (2)
	        isCommandReceived = 0;
	        HAL_GPIO_TogglePin(GPIOF, GPIO_PIN_1);
	        //HAL_Delay(1000);// (3)
            Motor1.setpoint = command.speed1;
            Motor2.setpoint = command.speed2;
            Motor3.setpoint = command.speed3;
            int speed=getthowerspeed(command.throwerSpeed);
           if(speed<3000)
           {
        	   TIM8->CCR1=3000;
           }
           else if(speed>6400)
           {
        	   TIM8->CCR1=6400;
           }
           else
           {
        	   TIM8->CCR1=speed;
           }

//            Motor1.kp=command.kp;
//            Motor2.kp=command.kp;
//            Motor3.kp=command.kp*4;

            //feedback.speed1 = TIM8->CCR1;
	        feedback.speed1 = Motor1.positionChange;
	        feedback.error=Motor3.Error;// (4)
	        feedback.speed2 =Motor2.positionChange;//Motor2.positionChange;
	        feedback.speed3 =Motor3.positionChange;//Motor3.positionChange;


	        CDC_Transmit_FS(&feedback, sizeof(feedback)); // (5)
	      }

  }
  /* USER CODE END 3 */
}

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


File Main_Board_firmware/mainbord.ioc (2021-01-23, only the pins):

Mcu.UserName=STM32G431KBTx
PA0.Signal=S_TIM2_CH1
PA1.Signal=S_TIM2_CH2
PA11.Signal=USB_DM
PA12.Signal=USB_DP
PA13.Signal=SYS_JTMS-SWDIO
PA14.Signal=SYS_JTCK-SWCLK
PA15.Signal=S_TIM8_CH1
PA2.Signal=S_TIM2_CH3
PA3.Signal=S_TIM2_CH4
PA6.Signal=S_TIM16_CH1
PA7.Signal=S_TIM17_CH1
PA8.Signal=S_TIM1_CH1
PA9.Signal=S_TIM1_CH2
PB4.Signal=S_TIM3_CH1
PB5.Signal=S_TIM3_CH2
PB6.Signal=S_TIM4_CH1
PB7.Signal=S_TIM4_CH2
PF1-OSC_OUT.Signal=GPIO_Output

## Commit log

2021-01-14 Main Board Bill of Material
    [Main_Board_BOM.csv]
2021-01-21 Main board image
2021-01-23 Main board and driver board firmware full
2021-01-27 main board
2021-01-27 Update on BOM
    [BOM of Main Board.xlsx]

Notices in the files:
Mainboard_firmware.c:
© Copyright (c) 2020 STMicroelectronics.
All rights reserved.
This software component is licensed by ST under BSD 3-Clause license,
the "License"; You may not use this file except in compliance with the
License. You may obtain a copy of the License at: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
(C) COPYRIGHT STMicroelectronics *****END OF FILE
